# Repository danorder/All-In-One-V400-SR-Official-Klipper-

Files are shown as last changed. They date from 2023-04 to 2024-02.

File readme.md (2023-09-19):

## Flsun V400/SR Overhaul in Accordance with Klipper Standards / Delta ## STATE UPDATING USE RELEASE links to the left ===============================================>>>>>>>>>>>>>>>>>>>>>>>>>>>>>>

Configuration Variants:
1. OFFICIAL Klipper: Raspberry Pi , BTTPI PAD7 or general Linux device. Otherwse reinstalled Speeder-pad with OFFICIAL Projects. 
2. Flsun Speederspad Klipper: Includes many changes to core Klipper files. - conflicting docs i wont make any Further updates due to tramming disabled / official klipper project "ban" / docs conflicts among other false posts about Official project issues.
This is simply to much hastle for users , devs and, the official klipper team to deal with daily.  

Note:
On some printers, it may be necessary to temporarily increase 'minimum_z_position' to -10 for the initial setup to run 'probe_calibrate' due to varying quality control. Once "calibrate macro completes the nozzle will be babystepped 0.2 high to avoid scrapes on pei if user manual probe_calibrate went a bit wrong simply babystep down frist print. if all went well the values is typically some range of 0.05-0.0-0.1. The first 'save_config' will add a section to 'printer.cfg' with calibrated overrides such as 'zoffset', 'delta_calibrate', etc. Furhter note. tramming (delta_calibrate)  does have limits it expects the printer to be well assembled / square to work. only then will bed mesh be "accurate" mesh is only a "supplement" to deal with slight topograpy issues with the bed. 
a delta should never rely on this. Ideally on a fully set up/fine tuned machine fade can be enabled and set to turn mesh off after the first few layers. This avoids the machine needing to constantly adjust z on every move. (this causes odd issues / artiiacts / dimension issues otherwise) If you feel you need more then 11 points, on mesh its time to check the machine for mechanical problems. 

What's New?
1. V400 trams in accordance with delta docs. if using "vanila" klipper of the website is installed." Otherwise not much from the original sr configs. 

2. Calibrate button: Runs endstop calibration, delta_calibrate, and bed_mesh. Use this button ONLY after running 'probe_calibrate' to set up the probe offset. The order of events remains absolute: set up probe offset, run 'delta_calibrate' to apply zoffset/tram the arms, and then run 'bed_mesh'. Preheat the bed to the printing temperature before running the calibrate button. The process is automated and will reboot/save on its own. It completes once 'bed_mesh' has finished. Fluidd/Mainsail will display the running procedure. After completion, the (babystep) will be 0.6mm high to avoid scrapes if the Zoffset is wrong. Simply (babystep) down from Mainsail or Klipperscreen during the first print.

3. Spread cycle and stealth chops: According to TMC docs, spread cycle is the most accurate but also louder. The mode can be set in start G-code or manually selected.
4. Safe homing.
6. TMC spreadsheet tuning.
7. Auto-saving baby step based on Mental's XYZ offset macro.
9. Raspberry Pi Pico ADXL support.
11. Properly functioning bed mesh.
12. Revised macros to remove redundancy.
13. Effector LED turns on when running G28.
14. RGB EFFECTOR PCB support
15. Filament drying
16. Profile overrides
17. Multiple effector / extruder support.
18. Tool change
19. Thermal runaway....is renabled.
20. Z velocity cannot crash into the bed at 600-400mms........
21. built in flow / rotation distance calculators
23. Automated calibration (endstop, delta_calibrate, bed_mesh). Preheat the bed before using this. The probe must be on.

Note: Links are also provided to credit various authors and, view their pages. Credit for any specific code or collaboration efforts can be found in the corresponding .cfg files.
The Flsun Facebook community sr/v4 community pages, KevinOConnor's Klipper 0.s, mainsail/fluidd teams, and KlipperScreen are acknowledged.

To date i haven't aprooved any copy pasted versions from the sr/v400 regarding github.  I also won't support these on fb since they only offer user confusion or unrelated bugs / personal time waste looking for unrelated problems or, problems i can't personally solve in github.   

No collabs have been done unless explicitly listed by name in conigs other then rootiest with some jinja on the updated calibration button.  
Note Use and improvements of open-source code are encouraged and appreciated other then personal clout. Reminder Always thank developers for their work, time, and support. Happy printing 

Support Links / credits 
- For further support: Facebook Group (https://www.facebook.com/groups/1502404840209556)
- Klipper official website: klipper3d.org (https://www.klipper3d.org)
- Mainsail UI documentation: docs.mainsail.xyz (https://docs.mainsail.xyz)
- Moonraker repository: github.com/Arksine/moonraker (https://github.com/Arksine/moonraker)
- Kiauh repository: github.com/th33xitus/kiauh (https://github.com/th33xitus/kiauh)
- Private users / testers / feedback.

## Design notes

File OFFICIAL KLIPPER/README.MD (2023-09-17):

Base files Pick the correct printer board and, remember to rename to printer.cfg 

`State in Testing ` Note not all docs may be up to date on "terms" this is in w.i.p state. 

`Sr / v400 are unified. the only difference will be pritnter.cfgs and start / end.`

REMINDER: TO RENAME WHATEVER BOARD TO printer.cfg 

`Import Notes:`
- `pid_tune` macros do not save_config to allow running both without double reboots.If `pid_bed` is enabled for "calibrate macro," 

-Both `virtual_sdcard` and `variables.cfg` locations may need to be changed. It depends on how Klipper was installed and what directories it's using. The assumption is it's using the `printer_data` directory and a "single install." Otherwise, tools like WinSCP or PuTTY can be used to find the "current" locations.

Since a clean config will have no calibration settings, a `bed_mesh` error will pop up and disappear after "calibrate" is run. 

To avoid cluttering macros, restore "mainsail" under settings with the provided `backup-mainsail.json` layout to put macros under categories.

`What's New?`
- `Filament_dehydrate` macro for use with a filament box or bed heater.
- SR firmware emulator/speed macros for non-dynamic acceleration or adjusting print speed during filament G-code. Use "active" in the pull-down menu to resume values after a reboot. These can also be used to speed up or slow down prints.
- Overhauled macros with pull-down menus available in Mainsail/Fluidd. Most macros use 1=on or 0=off.
- Filament flow/rotation distance calculators.
- `5 extruder/effector selection macros` for quick swaps or common mod support. The default will be v400 orsr effector on a fresh config Note: if using other effectors `printer.cfg macoro = config values`

- `Rotation distance` can be adjusted or saved with the `extrude_140` macro. A negative value will also reverse the motor direction. Note: this a global override and, will be the current value on boot.
unless changed with a `extruder/effector macro ` 

- Most macros display errors/hints in the print stats section or terminal.
- `Built-in slicer profile overrides`. By default, these are inactive until values are set. Profiles like PLA 100, PETG 94, etc can be used by saving required changes in the machine with `save_profile`

`To make a profile.` first put in the flow value this also doubles as selecting. e.g pla 100 flow , all retract values and, p.a.  Speed override is selecteded differently. use 1 in the "flow value" then whatever value more or less. e.g 120%. this will make the printer run 20% percent faster or 20% more of the profile. 
- `Firmware retraction` values per profile can be saved and used when a specific filament is chosen using `select_profile` macro, such as PLA.
- To use these either click `select_profile` macro and, select one. the value can be anything e.g `1` nothinng specific is assigned. This will load the profile and, also the selected profile will remain active until changed. 
E.g If pla is selected and, the printer is rebooted this will remain said retract / flow values on boot. These can either be used alone or callee in slicers with perfilament/gcode profiles such as ideamaker/prusa/supersslicer.
E.G  `select_profile PETG=1` would go in start_gcode or X slicers custom filament/gcode options. This should avoid to much reliance on slicers / faster settings changes. NOTE: Ensure slicers defaults on Flow are 100 or 1.0 and, Firmware retract is enabled. (Firmware retract is not required saved retract values wont work unless its enabled)
regular slicer retract can also be used and, Only the flow,p.a and speed modifer values will be used. FURTHER NOTE: 
To turn off profile overrides simply add any value to PROFILES_OFF.  This can also be put on end gcode to only use overrides on certain profiles. 
Tip: The variables file can be directly edited for faster chages on profiles settings or diagnostics. 

The `M500` macro lists "saved_variables" and displays things like current flow, rotation distance, input shaper, etc., in the terminal similar to marlin.
optionally you can open the variables file to view asigned values / change things like the flow/retract profiles.  

`Calibrate Macro Update:`
- The `calibrate` macro now attempts to run a `shaper_calibration`. If no shaper is found, it will display an error, reboot, and continue to the next calibration. The terminal will show this information if an ADXL is present or if the calibration failed.
- The `calibrate` macro has an option to change the default safe height in the pull-down menu. The default is 2mm high to avoid scrapes and should be lowered during the first print. The old default is 0.6mm high. The large height increase is to accommodate varying effectors/mods/probes.
- Regular `delta_calibrate`/`Probe_calibrate` behavior remains the same as on the website. If used in the terminal, these macros will not leave the nozzle high for the first print. ALWAYS reset "zoffset" before hand aka babysteps. 
- The "Calibrate Settings" macro currently has the option to enable PID tuning of the bed during the calibration routine. The default behavior is off on a clean config with no variables file.
It also includes the option to enable `shaper` or turn it off (useful for pritners with permanet adxls) value 1=on 0=off. 

Prime blob extrude amount/length can now be adjusted with the `prime_blob_settings` macro, which also allows for extrude speed. Note that speed values are in mm/s instead of mm/min for simplicity.

Other updates include Prusa support macros, adjustable values in the pull-downs for PID bed/hotend macros, and fan speed override (`m106` adjustment). Refer to the documentation at https://github.com/garethky/klipper-voron2.4-config/blob/mainline/printer_data/config/part-cooling.readme.md (created by the original author) for details on overriding fan speeds.

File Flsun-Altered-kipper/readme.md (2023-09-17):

`STATE LEGACY`

updated start gcode prime blob pattern.  tuesday march 14 2023 prime arc depreciated /default cura start. 

Designed to work with "pure stock speeder pads' (Flsun firmware)

Note: The klipper files are "modified" and, Klipper screen cannot set PROBE zoffset.  its using babystep which is just a workaround for slight probe_offset measurement issues with paper etc.  This will lead to strange deviation numbers due to not knowing the hardware offset. it will need to run  Probe_calibrate to set the Probe zoffset" This can be done from terminal. or, Klipperscreen returned to oem via reinstall.  Stock KlipperScreen will have a "zcalibrate" button with a Probe option. This is probe_calibrate which  will include  lower by X amount buttons to run the paper test vs use terminal. https://www.klipper3d.org/Bed_Level.html#the-paper-test
once this is done delta_calibrate needs to be run to both tram and, apply the new probe_offset then Bed mesh can be used afterwards. Note bed level 1 and 2 are replaced with Calibrate which will run everything except for probe_calibrate. The probe must be on first and bed temp should first be set to desired print temp. Running it will run all required calibration also saving / rebooting by itself. Lastly the Nozzle will be left 0.6mm high to avoid scrap potential. on the first print simply "babystep" down to set the first layer. Generally if Probe_calibrate was on point the babystep / zoffset will be 0.00 or close. 

`General instructions for files `

Simply rename or remove the current printer.cfg and, replace with github printer.cfg and, other_features files. The pico file / shaper file is optional but setup for a 
raspberry pi pico this can very depending on device. to enable there is a include near the top of printer.cfg removing the # will enable the file however after shaper is run using a pico the file will need to be disabled again otherwise the pico would need to be plugged into he pad at all times. (It would see the pico as another required printer mcu otehrwise)    

`Initial startup` will not have a "save_section at the bottom of printer.cfg" probe_calibrate will be required to run first , Then calibibrate button. note unless a nozzle is changed or somthing that would affect the probe / hotend height. Probe_calibrate generally doens't need to be run again just the calibrate button for general leveling or changing bed temps to account for mesh / height changes with thermal  expansion.  

`Note `if coming from sr configs the functioality is basically the same / procedures. 
put files on , with mainsail / fluidd do not copy paste use the file.. this often leads to formating issues for whatever reason. 

`REMINDER `when running anything to do with "probing" put the probe on first. Calibrate button probe on first same with probe_calibrate 
for extra clairity when using probe_calibrate once it probes the bed remove the probe then do the paper test. accept must be typed or hit before 
save_config. 

`#1` Probe_calibrate with terminal or oem Klipper screen. Note: klipper screen has a slight bug atm when using the zcalibrate button it will not save_config and, the prompt will just dissapear seemingly freezing. Simply save_config from fluidd/main this will solve it for now. 

`2.` Preheat bed to temps used for actual printing. 

`3. `Hit calibrate macro. This will run a automated calibration routine saving / restarting on its own it will finish after bed_mesh. 

`4. `The calibrate button will leave the nozzle 0.6mm high lower this during a print. this is to avoid usererror or dimension issues with paper setting zoffset with Probe_calibratate. 

`5.` Make sure to run bed / hotend pid.

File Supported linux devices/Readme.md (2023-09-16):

Known devicess that support standard installing and,Klipper documentation 

BTT PAD 7 
BTT PI 
RASPBERRY PI MIN 2.0 
RASPBERRY PI COMPUTE MODULE / PAD7 / OTHER ADAPTERS 

OFFICIALLY UNSUPPORTED DEVICES BY KLIPPER. 
SONIC PAD - 
SPEEDER PAD 
QIDI 

Exception. 

If the user can install / revert project to their supported state these would again follow docs / work with the website aka manual. 
However the con is installation remains much harder then it should be / time consuming,  you will also be missing critical features depending on boot loader such as 
bootable ssd/hdd

.  clonable able ssd /hdd 

.  standard mostly setup o.s images / project support

.  on some devices you have no fall back to data loss if bootable media is not removable. e.g devices blows up no sdcard etc to remove / get data off with pc. 
the only option is repair it. 

.  Well known issues and solutions. Exception social media pages may have the solution or may not con you have sift through opinions/missinfo  to find facts on the matter. or some solutions may not be up to date.  

.  Reliable and, trustworty updates  (updates should only be coming from ubuntu, or debian main servers for the o.s) Klipper and other installed projects only need to update with the updater in mainsail/fluidd

FLASH TOOls  RASPI-FLASHER this also has the option to download mainsailos for pi devices 
belena etcher , has sdcard cloning funcion. useful to update a bunch of printers or simply make backups. very useful for print farms / identical machines. 

WHY ARE THEY NOT SUPPORTED? 

In a nutshell devices not following the standard installation or original files simply are confusing users and, creating conflicting users posts / questions / assumptions. 

This leads to impossible to support scenarios and, forces the user to be ultra specific on questions that shouldn't be.  E.g we'd need to know the device , device changes , device problems and, if its a user error or the device at fault. 
to even begin to get started. 

Users become confused on where the problem is. and, the official projects get blammed for issues of 0 relation. 

Projects cannot solve / update issues that don't exist. 

These devices do not help the actual projects with dev or simple things like bug reports or new ideas. 

some devices have none standard ui leading to confusing ansewrs and questions in relation to buttons / commands. or, some buttons may have completly different behavior then expected. 

updates do not keep up eventually leaving the users far out of the loop. in some cases this could be a steep learning curve or require a good page read on recent changes found on the website.

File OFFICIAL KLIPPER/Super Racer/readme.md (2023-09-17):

Sr Firmware is identical to the v400 other then "build size / extruder" NOTE: GET BACKEND.CFG FROM THE PEVIOUS DIRECTORY THEY NEED THIS.  

If using extruderS macros use the printer.cfg MACRO THIS = default printer.cfg config values. everything else overrides printer.cfg unless set back to default with printer.cfg macro."

SETUP: 
Firstly rename xx sr board to printer.cfg. 2nd printer.cfg , backend , and, mainsail ui backup are required. simply drag and drop these on to mainsail. 
Due to varying hardware printer.cfg virtual sdcard and, variables location will most likely need to be adjusted. The old tutorial island aspect of the sr is now "depreciated" since forums have enough users now. 

Note calibration behavior / methods have not changed.  and, remainss  1. put on the probe 2. run probe_calibrate though terminal or klipperscreen (zcalibrate button) 3. preheat the bed 4. run "calibrate" wait for the
routines to complete. do not take off the probe it ends at "bed_mesh" rebooting a few times.  5. run pid hotend / bed. Note "babystep" will be left 2mm high. one the first print loweer this, this is to avoid scrapes. 
also Note only the calibrate button resets babystep. if using klipperscreen delta_calibrate/probe_calibrate. babystep must be reset prior as it does not do this otherwise the old value will be in affect. e.g if its stil
-2mm low this could be a scrape. 

refer to the main v400 folder release notes for further info since firmware is "unified" 

cura / prusa start gcode files have the required code.

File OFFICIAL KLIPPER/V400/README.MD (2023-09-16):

`State should be stable ` 
`Sr / v400 are unified. the only difference will be pritnter.cfgs and start / end.`

REMINDER: TO RENAME WHATEVER BOARD TO printer.cfg 
Configs by default assume official klipper device locations and, single install. (Not all projects keep in sync with multiinstall this requires a bit of manual setup.) 
make sure to check, Moonraker.conf has the correct location for your device. typically this printer_data btt partner devices use "biqu" instead of PI for user. so biqu/home. 

`Import Notes:`
- `pid_tune` macros do not save_config to allow running both without double reboots.If `pid_bed` is enabled for "calibrate macro," 

-Both `virtual_sdcard` and `variables.cfg` locations may need to be changed. It depends on how Klipper was installed and what directories it's using. The assumption is it's using the `printer_data` directory and a "single install." Otherwise, tools like WinSCP or PuTTY can be used to find the "current" locations.

Since a clean config will have no calibration settings, a `bed_mesh` error will pop up and disappear after "calibrate" is run. 

To avoid cluttering macros, restore "mainsail" under settings with the provided `backup-mainsail.json` layout to put macros under categories.

`What's New?`
- `Filament_dehydrate` macro for use with a filament box or bed heater.
- SR firmware emulator/speed macros for non-dynamic acceleration or adjusting print speed during filament G-code. Use "active" in the pull-down menu to resume values after a reboot. These can also be used to speed up or slow down prints.
- Overhauled macros with pull-down menus available in Mainsail/Fluidd. Most macros use 1=on or 0=off.
- Filament flow/rotation distance calculators.
- 5 extruder/effector selection macros for quick swaps or common mod support. The default will be v400 effector on a fresh config.
- `Rotation distance` can be adjusted or saved with the `extrude_140` macro. A negative value will also reverse the motor direction.
- Most macros display errors/hints in the print stats section or terminal.
- `Built-in slicer profile overrides`. By default, these are inactive until values are set. Profiles like PLA 100, PETG 94, etc can be used by saving required changes in the machine with `save_profile`
To make a profile. first put in the flow value this also doubles as selecting. e.g pla 100 flow , all retract values and, p.a.  Speed override is selected differently. use 1 in the "flow value" then whatever value more or less. e.g 120%. this will make the printer run 20% percent faster or 20% more of the slicers profile. 
- `Firmware retraction` values per profile can be saved and used when a specific filament is chosen using `select_profile` macro, such as PLA.
- To use these either click `select_profile` macro and, select one. the value can be anything e.g `1` nothinng specific is assigned. This will load the profile and, also the selected profile will remain active until changed. 
E.g If pla is selected and, the printer is rebooted this will remain said retract / flow values on boot. These can either be used alone or callee in slicers with perfilament/gcode profiles such as ideamaker/prusa/supersslicer.
E.G  `select_profile PETG=1` would go in start_gcode or X slicers custom filament/gcode options. This should avoid to much reliance on slicers / faster settings changes. NOTE: Ensure slicers defaults on Flow are 100 or 1.0 and, Firmware retract is enabled. (Firmware retract is not required saved retract values wont work unless its enabled)
regular slicer retract can also be used and, Only the flow,p.a and speed modifer values will be used. FURTHER NOTE: 
To turn off profile overrides simply add any value to PROFILES_OFF.  This can also be put on end gcode to only use overrides on certain profiles. 
Tip: The variables file can be directly edited for faster chages on profiles settings or diagnostics. 

The `M500` macro lists "saved_variables" and displays things like current flow, rotation distance, input shaper, etc., in the terminal similar to marlin.
optionally you can open the variables file to view asigned values / change things like the flow/retract profiles.  

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

Prime blob extrude amount/length can now be adjusted with the `prime_blob_settings` macro, which also allows for extrude speed. Note that speed values are in mm/s instead of mm/min for simplicity.

Other updates include Prusa support macros, adjustable values in the pull-downs for PID bed/hotend macros, and fan speed override (`m106` adjustment). Refer to the documentation at https://github.com/garethky/klipper-voron2.4-config/blob/mainline/printer_data/config/part-cooling.readme.md (created by the original author) for details on overriding fan speeds.

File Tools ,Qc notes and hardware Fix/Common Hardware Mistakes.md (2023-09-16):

Adxl 
These must be m mounted to a ridgid place. ideally in metal. Do not mount on plastic fan mount or on fans. (rattling bearings) The hole on the stock V400 duct is to get to the setscrews to remove the heatbreak. 
Btt does have a pcb for the extruder stepper Motor, fystec and similar placement is a bit more awkard.  

Belts make sure to check the pulleys on the top for belt deformation. this means belts are to tight, im still not aware of a correct and, documented spec way with guitar tuners. This does have a speciic method . e.g corexy with "gates brand belts"
(yes it matters) is axis back from the front measured 150mm pulley pin to tensioner pin at 100-110 hrz. The delta carriages would need somthing as specific also. 

Sr assembly does not have "centering pins" 
use a machinest square to check things over and, towers are not angled left / right.  always use a diaganol patern when installing / tightening screws.  if its 4 screws this would be a X pattern, This is for alignment reasons. 

Beds 
on the gen 1 and 2 sr (metal clamps) ensure these are not excessivly tight this is known to affect delta_calibrate/mesh. if to tight the bed may lift fighting the camps at certain temperatures (you need to check this
every priners differnt) e.g mine raises maybe 1-2mm at 80c, 

Stock sr hotends 
Expect to print higher temps then the rolls. namely if coming from slower printers your printing all around faster this ends up needing more. failure to do so commonly damages the extruder. This is a overtime affect
typically from excessive force trying to extrude. a bmg or similar gear box with full size stepper has more then enough torque to always extrude. The problem it will also backfire on itself possibly damaging the filament path or reducing the filament to a spring coming out the lever. Further part of the temp difference relates to the clone block thermistor placement, its not reading the nozzle like the real design, and, also the nozzle is stuck to far outside  the meltzone.

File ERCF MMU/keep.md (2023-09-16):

 Place holder coming soon 
 in advance recommended hardware. 
 1. mellow ercf board
 2. 2 binky pcb / encoder ( original is to unreliable with sourcing / calibration hastles)
 3. its possible the "2.0" will come out "soon" namely this will just be easier for users to assemble. however the 1.1 if assembled correctly / good print settings shouldn't offer much difference.

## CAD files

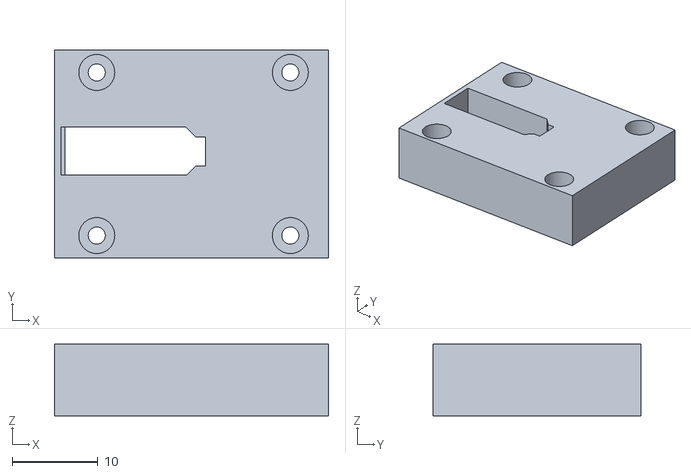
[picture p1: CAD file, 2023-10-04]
OFFICIAL KLIPPER/probe cover.stl
32.0 x 24.2 x 8.39

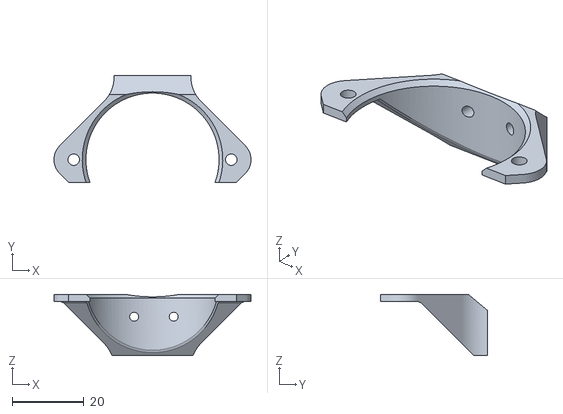
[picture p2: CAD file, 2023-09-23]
OFFICIAL KLIPPER/v400 adxl.stl
54.8 x 29.8 x 17.0

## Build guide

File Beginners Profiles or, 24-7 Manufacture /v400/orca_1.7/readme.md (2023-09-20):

REQUIREMENTS: 
current start / end gcode in official klipper directory
Firmware retract enabled 
Firmwawre flavor Klipper 

FLSUN V400 DEFAULT PROFILES. just import these. in the future it'll be custom machine to avoid problem / unwanted changes on updates. 

Profile Notes / intent 

Silk pla 0.1 = Max quality - Designed to deal with random prints / avoid ghosting. Brand cc3d metal rainbow silk.
Note: Damping feet required unless you like hop noise :/ 
Goes with cc3d material proile. (shoudld work for most silks) if not adjust temps etc. 

Petg 
red-green = 0.2 muliprint on bed , parts , cosmetics. Designed to always print, can be scaled up with feedrate (depending on filament viscosity) 
Note these colors are A-typically slower. "semi transparent will usually run quicker. This can also be used as a base / starting point for all colors otherwise. 

Black generally runs quite a bit faster note temps are typically on the low side, prone to showing extruder noise if printing to hot. (vertical line / diaganols /diamonds patterns) 

silver

ABS 

CF 

CF PETG 

CF POLCARB

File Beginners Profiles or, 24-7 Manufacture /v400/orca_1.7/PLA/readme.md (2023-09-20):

Note cc3d silk has custom gcode , if not using pritnerprofiles overrides. remove or turn off by adding a  " ;some gcodde is off " (no quotes just the ;)

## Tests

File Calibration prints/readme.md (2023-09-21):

Calibration prints / links / credits 

Official Klipper stls 
https://github.com/Klipper3d/klipper/tree/master/docs/prints

Thingiverse collection 

https://www.thingiverse.com/danorder68/collections/23166150/things

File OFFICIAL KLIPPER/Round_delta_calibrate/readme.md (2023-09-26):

Optional "klipper mod" / fix namely this avoids dented beds in the middle / adverges the middle and, follows a circle vs the pentagon. lastly the pentagon is offset a bit at the front / less then the back.
Note: This wont "solve" real mechanical related issues , eg. uneven belts , loose carriages  , unlevel probs to nozzle. etc. 

Simply open putty/winscp / whatever network file manager 

navigate to klipper then klippy then extras drop the file on / overwrite. or also copy it off, (you can get the file off klipper git / restore with update manager)
Note: this is simply a fast easy patch im not sure how long feature reqests will take / dev discussions.

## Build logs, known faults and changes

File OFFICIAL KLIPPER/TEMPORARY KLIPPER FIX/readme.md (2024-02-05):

SEMIREQUIRED FIX FOR KLIPPERS BOUNDRY CHECKS INVOLVING SPEED NAMELY THIS DOESN'T HAPPEN WITH "DEFAULT"S UNTIL AFTER THE BED. THIS LEADS TO GENERAL STABILITY ISSUES PRINTING TO FAST CLOSE THE EDGES AMONG OTHER ISSUES.

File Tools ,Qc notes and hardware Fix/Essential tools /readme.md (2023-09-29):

Basics everyone should have in general. 

Wire brush for nozzle cleaning

1.9-1-8mm (just under 2mm wire) for heagt break clog removal. some stores may havee thse. 

Machinest square to ensure axis is square / other parts 

Reasonable quality calipers 

Multimeter. Things happen eventually everyone should be able to at least runa continunity test for bad wires etc or verify things like heater wattage "claims"

 Good set of allen keys / Drivers / bits.  low quality keys just lead to stripped screws and, make assembly / maintainece take longer then it should.

 G900 or boron nitride. pc paste simply is not rated for hotend temps... all metal hotends heatsinks need optimal thermal transfer to avoid clogs. 
 Nitride can/will improve transfer on nozzle threads / heater cart / thermistor filling in the gaps. 

jst/xht crimps / crimpers  nothin magic about heaters or thermistors its typically better to order these in bulk or make minor repairs on other wires 

Good quality Soldering iron. t12 , hakko , aouya yihua "some" wellers" avoid the None digital mostly suited for wires
tinning solder - not quite the same as reg solder recoats the tip / restores it if badly oxidised 
no clean flux,  
63 ,37 solder
heatshrink
some type of helping hands. printed or bought

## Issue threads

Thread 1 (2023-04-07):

Printer.cfg Values

arshish1612, 2023-04-07:
Are these the correct values we should start with? Copied from your current printer.cfg file. Thq SQV is very different from what Klipper recomments as 5. Also Pressure advance is 0.

max_accel: 3185
max_accel_to_decel: 1875
max_z_accel: 1500
square_corner_velocity: 333

danorder, 2023-04-08:
Yes because a delta and should be able to take corners ideally without
limiting. Otherwise values can be set with slicer jerk depending on the
required situations. Pressure advance by default should always be 0 since
this is a material/brand specific setting. leaving a random p.a value
especially if not needed at all would most likely lead to scraping ,
overhang problems , and first layer adhesion issues.   Further the  klipper
manual is only a generic starting point for all settings to deal with the
plethora of machines which also applies to the "reference" configs on
github.  Lastly the good enough reference point  klipper leaves  up to user
to do the specifics. eg voron / ratrig are quite a bit more elaborate, not
much is left generic. . . . .

On Fri, Apr 7, 2023 at 3:12 AM Arshish Maneckji ***@***.***>
wrote:

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

arshish1612, 2023-04-11:
Few Questions:

1. Wont square_corner_velocity: 333 cause excessive smoothing?
2. Also - Should we change the ACCEL 7 Acceo_to_Decl values basis what the input shaper provides?
3. Currently cannot complete the input_shaper routine. getting this error: mcu 'mcu' shutdown: adc out of range

Closed 2023-04-28.

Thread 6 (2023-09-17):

Steppers (A,B,C) make a lot of noise after homing

seekis, 2023-09-17:
I was using the previous config and the steppers were silent all the time. I loaded this one up a few hours ago and now the steppers hiss or make a white noise like sound after homing or anytime they are holding. I figured out if I push the stealth chop button the sound goes away, but only until the next hold when I have to hit the stealth chop button again to silence the noise. Did I miss something?

danorder, 2023-09-17:
hmmm i'll take a look im assuming your on beta?

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

danorder, 2023-09-18:
I made a few small changes. to printer.cfg / backend if you mean beta and, not release.  Otherwise their should options in start/end gcod in the "release folder" . basically ive left both options possible.  one can just call spreadcycle or stealth chop in start to deal with print noise.  Im opting to return stealth chop as default "persay" and spreadcycle in other areas since this seems to range a bit on machines. but, basically  the hiss relates to psu voltage and wires (v400 12guage would be more ideal then double stepper wires powering boards)  so spreadcycle wants  these reasonably clean being more "analog" but there will always be a bit. stealth manages this with a number of internal auto compensation  measures being the  difference. you can also p.m me on fb for a potentially faster response / solutions.

seekis, 2023-09-18:
Not sure what you mean by beta and release. I am using the everything in the OFFICIAL repo. I was using a mix of your other  klipper repo and Guilouz's klipper repo and thought I should try to unify my config and noticed you had the new official repo up so I backed up my existing configs, which were working pretty well and loaded everything you posted.

I'll up date the printer/backend files and see if this cures the hissing.

seekis, 2023-09-18:
RESLOVED! No stepper hissing after homing or at any other position hold.

danorder, 2023-09-19:
Anything in the mainbranch is bleeding edge. anything "stable" currently is under the releases on the left hand side. so for the sr the leagcy branch is the "stable" currently. until i mark v3 "stable'

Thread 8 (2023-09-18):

SUPER RACER - Sherpa Mini Direct Drive Extruder w/LDO36STH20-1004AHG(XH

seekis, 2023-09-18:
I was using the [LGX Lite](https://github.com/danorder/Flsun-super-racer-Full-klipper-config-/blob/main/upgraded%20extruder%20configs/lgx-lite.cfg) config, but I am not sure where I am supposed to include this data within the new format. For the time being I am going to try using the stockV400 extruder profile and see how things go.

seekis, 2023-09-18:
just edited printer.cfg, create steppers folder in ../printer_data and loaded the 24v-0.7a-e.cfg file and included it in printer.cfg.

danorder, 2023-09-19:
p.m on facebook since it sounds like i need to just trouble shoot yours. / it'll just be quicker. and, moving he steppers shouldn't solve anything, it would mean its not seeing printer.cfg or its not seeing the right one

Closed 2023-09-18.

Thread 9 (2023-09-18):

SUPER RACER - Calibrate macro does not complete calibration steps

seekis, 2023-09-18:
Enstop calibration starts, but I get a `Unknown command:"SET_PIN"`error after each re-home. Firmware reboots and console shows `Running Delta_calibration ` and then `Delta_calibration complete`, but does not do the calibration. Also does not do bed_mesh calibration.

danorder, 2023-09-19:
This sounds related to your other problem. namely it doesn't have the variables file or know the location of it. basically if calibrate has a issue it'll end or do nothing to avoid. a endless loop.

andreamassaro9, 2023-09-23:
@danorder I have the same problem on Flsun SR with version 3 and main branch (the error is in backend, changing only this file all works well). With the version 2.5, that I'm actually using, it works like a charm.

danorder, 2023-09-23:
which linux device is this on, i may need to add a 4th option, for file
dirs.  older versions of installs have a symlink to the old directory which
could be it, since the sr is just pins file.

On Sat, Sep 23, 2023 at 11:26 AM andreamassaro9 ***@***.***>
wrote:

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

Skydea777, 2025-04-05:
Hey there, I also have the same Issue, just started my Klipper Journey with my SR(' ' 'Slightly' ' ' Modded), the Calibration Script sadly fails after starting the ... I think Endstop Calibration and the Restart. (Using Mainsail)
Now after each Firmware Rest I have following in my Console Log:
22:50:48
Delta_calibrate complete
22:50:48
Running Delta_calibrate

Without it doing anything.... it is just there for a couple moments and just does nothing.

Here is my Hardware:
Raspberry Pi 2B

And Software Versions:
OS: Raspbian GNU/Linux 12 (bookworm) -> Latest Updates and Firmware
Klipper v0.12.0-482-g2ec69ae3
mainsail v2.13.2
moonraker v0.9.3-72-g7cdcca3c

Release (The latest one):
"All-In-One-V400-SR-Official-Klipper-/releases/tag/v3.00"

Also the FlowCube stl is missing and some other things are kinda wonky.

Prusa start Makro Fails with the notice "Error evaluating 'gcode_macro _PRUSA_START_SR:gcode': jinja2.exceptions.UndefinedError: 'dict object' has no attribute 'BED'" -> So "BED" is not the correct Value, but I also tested FIRST_LAYER_BED_TEMPERATURE and other versions, I am kinda stuck =(
(Also Tried: Prusa Slicer, Super Slicer and Orca Slicer, all therse "Slicer" Flavors do not work)

I know you did not Update this for a bit, but your Guide helped me, even if the structure of everything is highly confusing and there is now Real Step my Step Guide so one can understand what one has to do.
BUT! I made it, thank you from my whole heart :)

Please tell me if I can somehow help

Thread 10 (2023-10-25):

V400 PIN for [fan] incorrect in STABLE branch

arshish1612, 2023-10-25:
printer.cfg in the stable branch has the PIn for [fan] incorrectly marked as PB5.

I guess it should be PB1?

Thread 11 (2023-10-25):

QUESTION: Calibrate does not heat bed?

arshish1612, 2023-10-25:
Do we have to manually heat the bed before running the CALIBRATE macro?

danorder, 2023-10-27:
yes to the temp you use for printing since we need to factor in thermal expansion. This is why it it'll wait for temps to stabilize per calibration cycle to avoid deviation on delta_calibrate / mesh as a further note.

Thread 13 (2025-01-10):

Enhanced Calibration not working

BergoUSA, 2025-01-10:
After making the change, running the enhanced calibration input, nothing happens. Klipper used to calculate then prompt to Save Config.

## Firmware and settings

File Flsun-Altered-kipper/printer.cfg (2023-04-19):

[include other_features_v400.cfg]
[include timelapse.cfg] #Load the camera recording function
#[include pico.cfg]
	   
# Mks robin nano make menu settings cpu STM32F103.
# select the 28KiB bootloader, and serial (on
# USART3 PB11/PB10) communication. 
# rename klipper.bin to Robin_nano35.bin found in the klipper folder under out using putty or winscp. note 2022-12-24 Klipper does not need to be reflashed
############################################################################################################################################################
[printer]
kinematics: delta
max_velocity: 400 #max print speed ,default is 400mm/s
max_accel: 3185
max_accel_to_decel: 1875
max_z_accel: 1500
square_corner_velocity: 333
max_z_velocity: 80
delta_radius: 152 
print_radius: 152 #max printable radius 150,set it to 152 to avoid error "out of range"
minimum_z_position: -5 #min z position nozzle won't go to the position which Z lower the vaule

[virtual_sdcard]
path: /home/pi/printer_1_data/gcodes #else stock pad path: ~/gcode_files or for single klipper / moonraker installs /home/pi/printer_data/gcodes For old mainsail/fluidos images /home/pi/gcode_files until moonraker is updated. 

[idle_timeout]
timeout: 1620 #45 mins before steppers and, heaters power down without activity. (This is also the time limit to do a filemnt change using M600 aka filament swap or alternativly filament runout.)

[mcu]
serial: /dev/serial/by-id/usb-1a86_USB_Serial-if00-port0
restart_method: command

[input_shaper]
shaper_type_x: mzv
shaper_freq_x: 51.4
shaper_type_y: mzv
shaper_freq_y: 52.8
damping_ratio_x: 0.75
damping_ratio_y: 0.75
############################################################################################################################################################
[thermistor flsun_thermistor] #ntc3950
temperature1: 25
resistance1: 86732.304 
temperature2: 190
resistance2: 561.122
temperature3: 260
resistance3:  155.017

[extruder]
step_pin: PD6
dir_pin: !PD3
enable_pin: !PB3
microsteps: 8
gear_ratio: 50:10
rotation_distance: 22.705860904
nozzle_diameter: 0.400
filament_diameter: 1.750
max_extrude_cross_section: 0.640
max_extrude_only_distance: 500
pressure_advance: 0.0 
max_extrude_only_accel: 1000
instantaneous_corner_velocity: 1000
max_extrude_only_velocity: 75.0
heater_pin: PC3
sensor_type: flsun_thermistor #Generic 3950 
sensor_pin: PC1
smooth_time: 0.2
min_temp: -5 # extruder min temp
max_temp: 315 # extruder max temp
control:pid
pid_kp: 19.545
pid_ki: 0.987
pid_kd: 96.747

[tmc2209 extruder]
uart_pin: PD9
run_current: 0.900
hold_current: 0.01
stealthchop_threshold: 0
interpolate: true  

[gcode_macro UNLOAD_FILAMENT] #unload filament
gcode:
    save_gcode_state name=unload 
    G92 E0 
    G1 E5 F200
    G1 E-100 F800
    restore_gcode_state name=unload 

[gcode_macro LOAD_FILAMENT] #load filament
gcode:
    save_gcode_state name=load 
    G92 E0 
    G1 E50 F800
    G1 E40 F200
    restore_gcode_state name=load 

############################################################################################################################################################
[stepper_a]
step_pin: PE3
dir_pin: PE2  
enable_pin: !PE4
microsteps: 64
#microsteps: 16 # Enable this and, disable 64 to run input shaper. in some cases klipper will report a error with the adxl just run the shaper_calibrate command again. 
rotation_distance: 40
endstop_pin: ^PA15
homing_speed: 80
homing_retract_dist: 0
position_endstop: 415 
arm_length: 345 

[tmc2209 stepper_a]
uart_pin: PD5
run_current: 1.138
driver_HSTRT: 0
driver_HEND: 3 
sense_resistor: 0.110
interpolate: False 
stealthchop_threshold: 0  # 999999
############################################################################################################################################################
[stepper_b]
step_pin: PE0
dir_pin: PB9  
enable_pin: !PE1
microsteps: 64
#microsteps: 16 # Enable this and, disable 64 to run input shaper. in some cases klipper will report a error with the adxl just run the shaper_calibrate command again. 
rotation_distance: 40
endstop_pin: ^PA12
homing_speed: 80
homing_retract_dist: 0
					
[tmc2209 stepper_b]
uart_pin: PD7
run_current: 1.138
driver_HSTRT: 0
driver_HEND: 3 
sense_resistor: 0.110
interpolate: False 
stealthchop_threshold: 0  #999999
############################################################################################################################################################
[stepper_c]
step_pin: PB5
dir_pin: PB4  
enable_pin: !PB8
microsteps: 64
#microsteps: 16 # Enable this and, disable 64 to run input shaper. in some cases klipper will report a error with the adxl just run the shaper_calibrate command again. 
rotation_distance: 40
endstop_pin: ^PC4
homing_speed: 80
homing_retract_dist: 0
					

[tmc2209 stepper_c]
uart_pin: PD4
run_current: 1.138
driver_HSTRT: 0
driver_HEND: 3 
sense_resistor: 0.110
interpolate: False 
stealthchop_threshold: 0  # 999999
############################################################################################################################################################
#                     Fans / heaters /sensors 
############################################################################################################################################################
[fan]
pin: PB1
cycle_time: 0.00004

[heater_fan heat_sink_fan] 
pin: PB0
heater_temp: 50.0
cycle_time: 0.00004

[verify_heater extruder] 
max_error: 160 #default 120  #changed from original "stock flsun values"  to nearly stock klipper due to firesafety concerns / not triggering. (the 40watt heater is just enough to wwork) and, the reason for chtclone nozzles.  
#hysteresis: 5
#   The maximum temperature difference (in Celsius) to a target
#   temperature that is considered in range of the target. This
#   controls the max_error range check. It is rare to customize this
#   value. The default is 5.
heating_gain: 1
#   The minimum temperature (in Celsius) that the heater must increase
#   by during the check_gain_time check. It is rare to customize this
#   value. The default is 2.

[thermistor flsun_bed] #ntc3950
temperature1: 25
resistance1: 96133.006 
temperature2: 50
resistance2:  31350.574
temperature3: 100
resistance3:  3999.966

[heater_bed]
heater_pin: PA0
sensor_pin: PC0
sensor_type: flsun_bed #Generic 3950 # table or (flsun ntc3950) calibrated to +/-5 Note note stock 3950 tables were doen for amazon 5 packs hence "generic"" 
smooth_time: 0.7
min_temp: -5
max_temp: 120 #hotbed max temp
control: pid
pid_kp: 74.835
pid_ki: 2.711
pid_kd: 516.364

[temperature_sensor Armv7 mcu] #the temp of pad
sensor_type: temperature_host
min_temp: 10
max_temp: 100

[temperature_sensor mcu_temp] #the temp of mcu
sensor_type: temperature_mcu
min_temp: 0
max_temp: 100

[output_pin LED_pin]
pin: PE12
pwm: False
value: 0 # 0 = off ,1 = on


[output_pin LED_logo]
pin: PD11
pwm: False
value: 1

[filament_switch_sensor filament_sensor]  
pause_on_runout: True
runout_gcode:
 PAUSE
  M400 #Wait for current moves to finish: 
  M117 Ejecting remaining filament
  G0 E-0.5 F300  
  G0 E-51F1200  #eject remaining filament 0 
  #insert_gcode: RESUME  
switch_pin: PA4

################################################################################################################
##                              Probe /Tramming / Mesh settings                                                ##
################################################################################################################
[delta_calibrate]
radius: 145
horizontal_move_z: 30 
Speed: 100

[probe]  
pin: !PA11
x_offset: 0 
y_offset: 0 
z_offset: 16.00 #the distance between nozzle and level switch
speed: 4 
lift_speed: 15
Sample_retract_dist: 6
samples: 3 #probe one point three times get an average
samples_result: average  
sample_retract_dist: 3 
samples_tolerance: 0.01 # 
samples_tolerance_retries: 10 
					  
[bed_mesh]  
speed: 150 
horizontal_move_z: 30 #This value is related to the lift height of the nozzle during bed_mesh
mesh_radius: 145  
mesh_origin: 0,0  
round_probe_count: 9 # 7*7
mesh_pps: 4,4
algorithm: bicubic
move_check_distance: 3
split_delta_z: 0.025
	  
#fade_start: 1
#fade_end: 15
relative_reference_index: 24 #16 # Mesh values: 6=5 points 24 = 9 point Its better to use  less points in most cases unless dealing with extreamly  uneven surfaces eg slight bubled stickers , chunky powercoat etc  
#############################################################################################################
##                                           Effector & logo Led                                           ##  
#############################################################################################################
[gcode_macro led_on]
gcode:
  SET_PIN PIN=LED_pin VALUE=1

[gcode_macro led_off]
gcode:
  SET_PIN PIN=LED_pin VALUE=0

[gcode_macro logo_on]
gcode:
  SET_PIN PIN=LED_logo VALUE=1
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

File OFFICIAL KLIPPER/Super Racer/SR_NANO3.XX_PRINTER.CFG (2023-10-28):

[include backend.cfg]
[include timelapse.cfg] #Load the camera recording function
#[include adxl_boards.cfg] #pi pico this requires users enable whichever they have. 

# This file contains common pin mappings for MKS Robin Nano V3
# boards. To use this config, the firmware should be compiled for the
# stm32f407. When running "make menuconfig", select the 48KiB
# bootloader, and enable "USB for communication".
# The "make flash" command does not work on the MKS Robin. Instead,
# after running "make", copy the generated "out/klipper.bin" file to a
# file named "Robin_nano_v3.bin" on an SD card and then restart the
# MKS Robin with that SD card.
############################################################################################################################################################
###         MACHINE ABSOLUTE LIMITS / MOTION CONTROL / CONNECTED MCUS#/  ADD A # TO DISABLE MCU IF YOU DON'T HAVE ADXL OR PACKAGES INSTALLED             ###
############################################################################################################################################################
[printer]
kinematics: delta
max_velocity: 300
max_accel: 3700  #3000-9000-20000 after tuning with adxl / inputshaper stay to lower values otherwise starting out. eg 6000 note marlin default is 2800 this may work better on some printers or filament types 
max_accel_to_decel:3200 #I AM HALF MAX SET ACC BY DEFAULT. I CONTROL ZIG ZAG MOVEMENTS AND ADJUST VELOCITY BASED ON DIMENSIONS AND SMOOTH THINGS OUT. SET TO MAX WOULD BE SIMILAR TO MARLIN BEHAVIOR ADXL WIL COVER ROUGH MOVEMENTS. INCREASING MAX ACC IS USUALLY THE BETTER SOLUTION. 
max_z_accel: 3700 # this default should be fine / max acceration for z moves. (It may help to bump this up or down a bit depending on desired noise / zhop height. 
minimum_z_position: -25 #Once you find your z offset it is suggested to return this to 0 to avoid potentially crashing a nozzle for whatever reason. z offset shouldn't change unless the hotend has been adjusted. most things are flow related. 
square_corner_velocity: 31 # This can depend on desired speed to quality. higher values 15 -20 generally work fine. Left as a safe default. acc / corner velcoity can be adjusted with slicer controls macros handle this. i use a default of 15-30 or dynamic values. 
delta_radius: 130 #151.62 ish should show up after delta caibrate in the save section. 
print_radius: 130 #

[firmware_retraction] # make sure to enable this in slicer. cura printer settings addon is required to hit the check box. every other slicer should have it in settings tab. this allows live adjustments or ability to fix a mistake without canceling. 
retract_length: 6.5
retract_speed: 40
unretract_extra_length: 0
unretract_speed: 40
############################################################################################################################################################
###                                                   MAINBOARD / Device specific sensors                                                               ###           
############################################################################################################################################################
[mcu]
serial: /dev/serial/by-id/usb-Klipper_stm32f407xx_260044001651303239383037-if00 # Run ls /dev/serial/by-id/* on your Raspberry Pi to get YOUR serial or it wont connect

[virtual_sdcard]
#path: /home/pi/printer_1_data/gcodes #else stock pad path: ~/gcode_files or for single klipper / moonraker installs /home/pi/printer_data/gcodes For old mainsail/fluidos images /home/pi/gcode_files until moonraker is updated. 
path: /home/pi/printer_data/gcodes 
#path: /home/biqu/printer_data/gcodes #btt devices by default use Biqu as user keep note of this. 

#[temperature_sensor rpi_temperature]
#sensor_type: temperature_host

[temperature_sensor mcu_temperature]
sensor_type: temperature_mcu #note remove this for skr1.3 configs 

[save_variables]
filename: /home/pi/printer_data/config/variables.cfg  ############ THIS IS TO BE CHANGED AND SET TO THE SAME PRINTER.CFG DIRECTORY IF DIFFERENT. default pi/vanilla single install
#filename: /home/pi/printer1_data/config/variables.cfg  ############ THIS IS TO BE CHANGED AND SET TO THE SAME PRINTER.CFG DIRECTORY IF DIFFERENT. default pad/multiinstall. 
#filename: /home/biqu/printer_data/config/variables.cfg  ############ THIS IS TO BE CHANGED AND SET TO THE SAME PRINTER.CFG DIRECTORY IF DIFFERENT. (bique pad)
			 						  
[idle_timeout]
timeout: 1620 #45 mins before steppers and, heaters power down without activity. (This is also the time limit to do a filemnt change using M600 aka filament swap or alternativly filament runout.)


[input_shaper]   #PLACE HOLDER VALUES 
shaper_type_x = ei
shaper_freq_x = 0
shaper_type_y = ei
shaper_freq_y = 0

############################################################################################################################################################
### Extruder Configuration                                                                                                                               ###
############################################################################################################################################################
[extruder]
step_pin: PD6
dir_pin: !PD3
enable_pin: !PB3
microsteps: 32
rotation_distance: 7.71 #stock bmg. gear ratio depreciated for use of effector swap buttons. if using gear ratio values simmply convert  current value divide by gear ratio. e.g 20 / 3:1 or 3/1 =3 so 20/3 = value
full_steps_per_rotation: 200 #CHANGE ME TO 400 FOR 0.9 DEGREE Steppers  ROTATION DISTANCE WILL AUTOMATICALLY BE CALIBRATED THIS APPLYS TO STEPPING AS WELL NO CHANGES REQUIRED. 
nozzle_diameter: 0.600
filament_diameter: 1.750
heater_pin: PE5
sensor_type: Generic 3950 
sensor_pin: PC1
max_extrude_only_distance: 800.0
control: pid
pid_Kp: 15.17 
pid_Ki: 1.02
pid_Kd: 56.27
min_temp: 0
max_temp: 300 #this value is set high for the purpose of hot tightening the hotend. stock hotends / tubes will degrade rappidly past 245. burning ptfe is also a neurotoxin. 
pressure_advance: 0 #set this from the slicer / fluidd / Mainsail. or start gcode its easier to do this in slicers with material specic gcode functions. 0.1-1.5 layer hight isn't usally benificial. 
pressure_advance_smooth_time: 0.040
max_extrude_only_distance: 800.0
instantaneous_corner_velocity: 2.5 # The equivalent of extruder jerk. this does not speed up pressue advance like linear adance in marlin. higher values may improve bowden retract. eg 15 left slow as a safe default. 
max_extrude_only_accel: 8300 

[tmc2209 extruder]
uart_pin: PD9
interpolate: false #This can usually be enabled without causing issues to reduce noise.
run_current: 1.100
hold_current: 0.1
#stealthchop_threshold:999999 #optional depends on setup and how much noise from the case is considered acceptable. simply printing a stepper mount and hanging e off a cable eliminates the case noise. 


[gcode_macro LOAD_FILAMENT]
gcode:
    {% set slow_purge_speed = (4 *60) %}  #values converted to mms 
    {% set default_load_speed = (20*60) %}
    {% set slowload = (40) %}
    {% set fastload = (458) %}
    {% set svv = printer.save_variables.variables %}
    {% if svv.slight_purge_amount and svv.extruder_load and svv.slight_purge_speed and svv.filament_load_speed %}
    SAVE_GCODE_STATE NAME=load_state
    M117 loading filament...
    G91
    G92 E0
    G1 E{svv.extruder_load} F{svv.filament_load_speed} # fast-load
    G1 E{svv.slight_purge_amount} F{svv.slight_purge_speed} # purge
    M400 
    M117 loading filament complete 
    NEOPIXEL_DISPLAY LED=effector TYPE=extruder MODE=green
    G4 P10
    NEOPIXEL_DISPLAY LED=effector TYPE=extruder MODE=white 
    RESTORE_GCODE_STATE NAME=load_state
    {% else %}
    SAVE_GCODE_STATE NAME=load_state
    M117 loading filament...
    G91
    G92 E0
    G1 E{fastload} F{default_load_speed} # fast-load
    G1 E{slowload} F{slow_purge_speed} # purge
    M400 
    M117 loading filament complete 
    NEOPIXEL_DISPLAY LED=effector TYPE=extruder MODE=green
    G4 P10
    NEOPIXEL_DISPLAY LED=effector TYPE=extruder MODE=white 
    RESTORE_GCODE_STATE NAME=load_state
    {% endif %}
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

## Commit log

2022-12-24 Create start gcode latest klipper
2023-02-14 add thermistors / minor bug fixs with unload/load
    [printer.cfg]
2023-02-14 update thermistors / unload load minor fix
    generic 3950 tables arent accurate enough.
    [printer.cfg]
2023-02-27 several fixs update to stable.
    [printer.cfg]
2023-02-27 update to current release. several small fixes.
    [printer.cfg]
2023-02-28 update tmc rms fix stock flsun thermal runaway...
    [printer.cfg]
2023-02-28 set spread cycle default
    [other_features_v400.cfg]
2023-02-28 update / add tmc performance
    [other_features_v400.cfg]
2023-03-09 Update start gcode latest klipper
2023-03-15 Update and rename start gcode latest klipper to start gcode
2023-03-30 add v400 robin 3.xx
    [printer.cfg]
2023-04-18 Fix compare tool errors
    [printer.cfg]
2023-04-23 update primeblob
    [other_features_v400.cfg]
2023-04-23 reintroduce firmware retract
    [printer.cfg]
2023-06-06 fix typo in #notes
    [printer.cfg]
2023-06-06 Create printer.cfg
    add initial release subject to change etc
    [printer.cfg]
2023-06-07 Create printer.cfg
    beta upload not yet tested.
    [printer.cfg]
2023-06-11 Update other_features_v400.cfg
    fix { on pid bed default action.
    [other_features_v400.cfg]
2023-08-08 Update other_features_v400.cfg
    Fix a number of minor macro issues.
    [other_features_v400.cfg]
2023-08-09 Update other_features_v400.cfg
    several updates add more profile options. status draft
    [other_features_v400.cfg]
2023-09-05 Update backend.cfg
    Fix white led not turning off.
    [backend.cfg]
2023-09-09 Create Torque drivers
2023-09-09 Update Torque drivers
2023-09-12 Create printer(upgrade nano3.1).cfg
    [printer(upgrade nano3.1).cfg]
2023-09-12 Create V400 UPGRADE BOARDS
2023-09-19 Update backend.cfg
    add shaper settings
    [backend.cfg]
2023-10-01 Update printerstock.cfg
    Fix fan pin
    [printerstock.cfg]
2023-10-12 Update backend.cfg
    fix shaper calibrate option in dellta_calibrate. change neopixel pin
    [backend.cfg]
2023-10-28 Update SR_NANO3.XX_PRINTER.CFG
    enable input shaper to solve issue with backend.
    [SR_NANO3.XX_PRINTER.CFG]
2024-02-27 Update backend.cfg FIX SR PRIME BLOB ORCA SLICER.
    [backend.cfg]
